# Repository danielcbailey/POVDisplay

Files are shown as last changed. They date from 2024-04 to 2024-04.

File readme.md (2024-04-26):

# POV Display

This project uses a custom PCB with an RP 2040 to control 128 RGB LEDs. The LEDs are driven
by 16 high-speed PWM LED driver ICs. The system is cabable of full-color video playback.

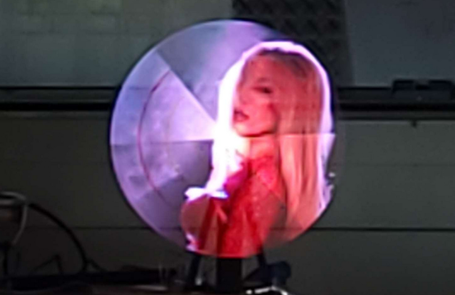
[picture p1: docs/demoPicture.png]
Picture of POV Display in Action


## Sections

[Embedded Software](#embedded-software)

[Video Generation](#video-generation)

[PCB Design](#pcb-design)

[Mechanical Construction](#mechanical-construction)

[Demo Video](#demo-video)

[Known Limitations](#known-limitations)

## Embedded Software

The RP2040 is an ARM M0+ microcontroller with two cores. The embedded software uses both cores
and has one preparing frame buffers while the other sends the data out at the right timing.

The system has two buffers for holding frames and will prepare the next buffer while the current
is read by the other core. The embedded software is designed to be as dumb as possible because
what dumb things lack in intelligence, they have in speed. There are only about 100 clock cycles
between bytes getting written out, so you won't see much code in the embedded software as every
line detracts from the needed speed.

#### File Reading

As such, the file that populates the frame buffers is designed to be as easy as possible for the
embedded code to read and display to the LEDs. The file is set up in such that all it has to do
is read the contents of each frame into the buffer, give a different pointer to each group (more
on this later), and send bytes to each group at the right interval. [Learn more about the binary file format](docs/fileFormat.md)

#### LED Output

The LED output core has three functions: 1. Send data to the right SPI peripheral at a specific
interval. 2. Update the interval based on how fast the board is rotating. 3. Request new frame
buffers when the current is exhausted.

#### Sending Data at a Specific Interval

There are four SPI channels for different regions of LED drivers (see PCB section for motivation).
They are controlled by PIO state machines with FIFO buffers enough to accommodate the entire
burst of data to all four ICs (8 bytes total). Given that bursts are so small but also don't fit
in 32 bits, they aren't well suited for DMA transfer as it would require setting up a new DMA
transfer for every 8 bytes - which comes with the setup overhead.

The RP2040 gives 2 FIFO buffers that can store 4 words of data. In this case, a word is defined
as a single byte, but the RP2040 allows for both FIFOs to be combined into one which allows the
burst to fit into a FIFO. This is key for meeting the timing requirements because the processor
doesn't need to wait for each bit to get written to the wire. By writting to each group's FIFO
buffers 32 bytes at a time, this gives much more headroom for the other activities while still
staying on time.

The actual timekeeping is using the 64-bit system timer which counts for each microsecond that has
passed. Usually, it needs to send a new burst every 25 microseconds, however an even number is
impossible to achieve because the exact timing depends on the rotational speed of the PCB. This
leads to small rounding errors which over the course of a frame consisting of ~41666us can lead to
up to 1.66ms of error in the timing over the course of the frame. This may sound small but it means
the frame can be off by as much as 7.2 degrees which will cause a visual oscillation.

Sub-microsecond precision is needed to stave off these unwanted side effects, and it accomplishes
this by multiplying the timer output by 32 (bit shifted, more precisely by 5 left). This gives 32
times the precision in terms of round-off error. Although floating point logic would eliminate
this need, the floating point calculations alone would easily consume all the clock cycles (3200)
that the loop needs to stay inside.

#### Updating the Interval

No matter the numeric precision of timing is, there will always be some error due to the mechanical
motion. Even a tight PID loop will have *some* error, so the interval update is a little more
complicated than dividing rotational period with number of bursts to write. The software tries to
blend the error so that it speeds up the next frame to make up for a slower current frame, or vice-
versa. This makes error easier on the eyes and looks like a shakey image as opposed to black regions
or chopped-off sections.

The software knows the rotational rate from a hall effect sensor mounted under the PCB. The sensor
provides a digital signal whether the magnet is in range or not, with some hysteresis. The software
measures when the magnet is in range and when it goes out of range. It corrects for the hysteresis
and finds the true center to align the frame vertically.

#### Requesting a New Frame

When the buffers are exhausted, it gets the next buffer filled from the other core. During this time
it applies the updated interval.

## Video Generation

Since the display itself just blindly reads from the file, the difficult task of generating the
video is moved offline to a more powerful computer where real-time conversion isn't necessary. Enter
the video encoder. View the code at tools/videoEncoder

#### Video Input

The encoder accepts any normal cartesian video (as opposed to polar like what it generates) and first
converts it into a series of still frames. This process is almost trivial thanks to [FFmpeg](https://ffmpeg.org/).

#### Frame Encoding

Next, the encoder converts each frame. To improve encoding performance, it does this independently
of previous frames allowing for parallelization. This leads to a decreased quality of output, see more
in the known limitations section.

The encoder simulates the path of the LEDs. It models the position of each one as it steps through
2000 values for angles of the PCB. The LED controller ICs expect packets of 2 bytes each, where the
first byte is the command and the second is the value. This allows us to control any LED and channel
at each step with few constraints.

The value may not be immediately appearent, however imagine that there is a scene with a red dress.
All the channels for each LED is likely to change often, however the red will change more because it
is the dominate color of that portion of the image. This allows us to change the red channel more
often than the others which visually gives a boost of detail and preserves contrast even if not 100%
color accurate.

Not only can it do this per-channel, but it can also do this per-LED for each controller IC. So what
software does is give each timestep a budget to change an LED. As each step passes, the available
budget is incremented by the timestep budget. It evaluates if it has enough budget to change a value
and if so, it samples LED colors and finds the channel that is most desperate to change. It generates
the command/value pair and adds it to the bursts it has generated and decrements the budget. This
mechanism allows it to optimize the bandwidth of the SPI SD card interface while "compressing" the
video.

LEDs are sampled by drawing a small arc representing the LED's path. This arc is drawn in a small
scratch image used for obtaining alpha values for each pixel. It then uses these alpha values to
sample the original image at the corresponding location to form a weighted-average to allow for
anti-aliasing of sorts.

#### Frame Rendering

To preview what the video will look like on the display, the video encoder will render each frame
by reading the sequence of bursts generated as if it were the display. It then draws each arc on
the work-in-progress frame. Since the real display takes advantage of interlacing the LEDs, the
render process will also draw the previous frame interlaced with the current.

These frames are stitched together using FFmpeg to form the preview video.

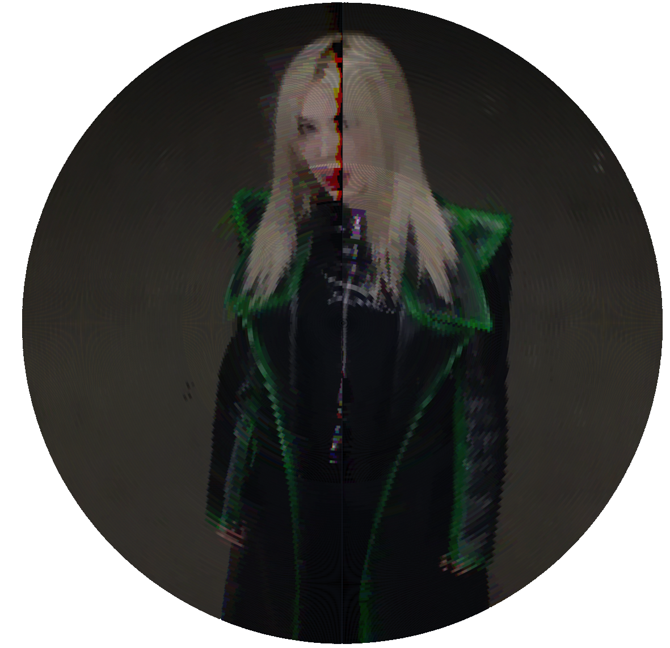
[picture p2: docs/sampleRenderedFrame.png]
Sample Rendered Frame


#### File Generation

Lastly, it generates the output file from the bursts generated during the encoding phase. It builds
the file by adding the headers and keeping to the format outlined [in this format](docs/fileFormat.md).
It does, however, add a small intermediate step. When copying the bursts over, it modifies the values.

The human eye does percieve luminous intensity linearly, rather it is an exponential relationship
where the eye is more sensitive to changes in intensity when light is dim than when it is bright.
The software applies correction for this by sampling from a lookup table and interpolating between
entries.

## PCB Design

The PCB was designed in Altium Designer. You can view the design files in the pcb/ folder. As mentioned,
the design uses an RP2040 at the center. It is connected to a microSD card slot with hardware SPI pins.
A digital hall effect sensor tells the microcontroller when the board has passed the vertical position.

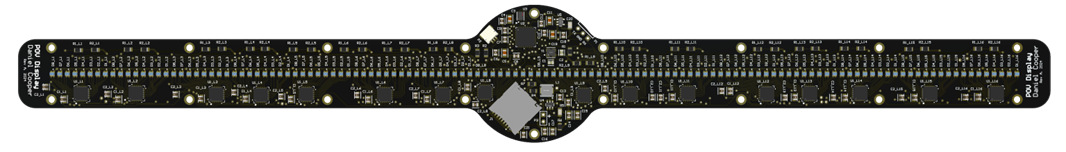
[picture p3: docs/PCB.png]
PCB Render


#### LED Controllers

After conducting an extensive search for LED controller ICs, I settled on the PCA9957HNMP from NXP. It
offers daisy-chain connection, SPI interface (that acts like a shift register while CS is held low), and
most importantly - high speed PWM at 31kHz. Most LED controller ICs have 10+ bit PWM but not only does that
not align well in the memory of the microcontroller, but it makes them slower. The speed comes at the
expense of color quality at low intensities, but speed is most important for a fast-spinning device like
this. The LED controller ICs also have constant current drivers for calibrating the colors and controlling
brightness without sacrificing PWM resolution.

#### Power Rails

The PCB is intended to be powered externally with a device such as a slip ring with 5-6V. A low dropout
linear regulator provides the 3.3V to the digital ICs, and a separate switching regulator provides 3.7V
for the LEDs.

## Mechanical Construction

The mechanical construction is crude, so I won't detail it much. The most notable component is the slip
ring that allows the board to continuously rotate without tangling wires. A small DC motor is connected
with a belt drive to spin the assembly. This DC motor is driven by an external circuit that performs
closed-loop control of the motor using PID. Ideally, a brushless motor would be used with a precision
driver, but I honestly didn't expect the rest of the project to work out as well as it did within the
time constraints.

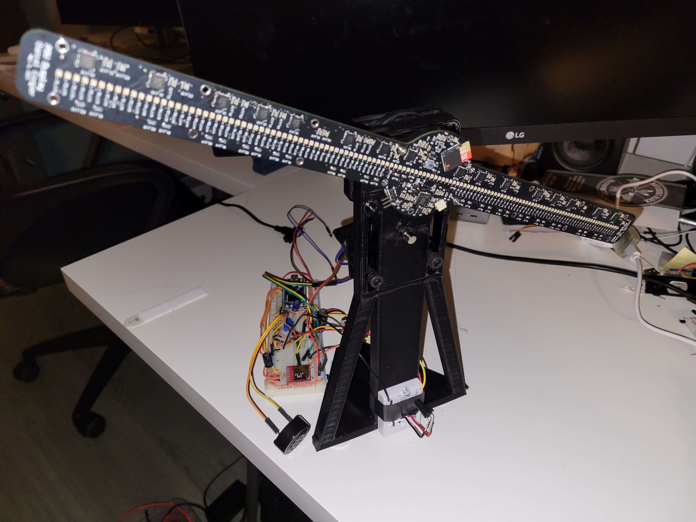
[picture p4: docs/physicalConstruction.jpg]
Mechanical Construction


## Demo Video

Coming soon!

## Known Limitations

Although the project has exceeded my expectations, it does have some notable limitations for those who
come across my work.

* The SPI interface for SD cards is slow (~11Mbps max) and it is the limiting factor for resolution and framerate.
Consider using a microcontroller that has an sdio interface.
* The power traces are not sized properly for the current ripple caused by the LED PWM. Make larger PCB traces and
larger bypass capacitors to not cause excessive ripple on the ground net.
* Consider using a servo motor for precision speed control. The image shakes a little still.
* Instead of using a slip ring, inductive power transfer would be better because I am exceeding the rated speed of
the slip ring by over a factor of two.
* Wireless communication such as WiFi would allow debugging while spinning, and upload of files to high-speed flash
memory (so that the SD card doesn't fly out).
* The PCB doesn't natively interlace the LEDs. I have performed this by mechanically offsetting the PCB, but this
leads to a slight imbalance.

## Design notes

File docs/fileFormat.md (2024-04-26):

# File Format of Video Data

The processor loads the data for the LEDs at any given time from the SD card.
The LEDs are in groups of four, and at any given transfer, one LED from each controller
must get updated. The timing of sending the data out can vary intra-frame and between frames.
This allows for variable resolution where it counts to get around the SD card limitations.

## Format Overview

The file is organized into the following portions:

* File header - details how many frames are in the file.
* Frame - the organizational unit for one complete revolution of the display. Frames contain four groups.
* Group - the organizational unit within one frame that details the data to be sent to one group of LEDs for that frame.
* Packet - the lowest-level container of data, corresponding to data samples and the rotational proportion they represent.

## File Header Format

| Offset | Field |
| --- | ----- |
| 0x0000 | File Format Identifier: "CRV\0" |
| 0x0004 | Number of frames: uint32 |
| 0x0008 | Start of frame 0 |

## Frame Format

| Offset | Field |
| --- | ----- |
| 0x0000 | Group 2 offset: n (uint32) |
| 0x0004 | Group 3 offset: m (uint32) |
| 0x0008 | Group 4 offset: p (uint32) |
| 0x000C | Frame length: uint32 |
| 0x0010 | Start of group 1 |
| n | Start of group 2 |
| m | Start of group 3 |
| p | Start of group 4 |

## Group Format

| Offset | Field |
| --- | ----- |
| 0x0000 | Number of packets: uint32 |
| 0x0004 | Start of packet 0 |

## Packet Format

| Offset | Field |
| --- | ----- |
| 0x0000 | Start of burst 0 |
| 0x0004 | Last bytes of burst 0 |
| 0x0008 | Start of burst 1 |

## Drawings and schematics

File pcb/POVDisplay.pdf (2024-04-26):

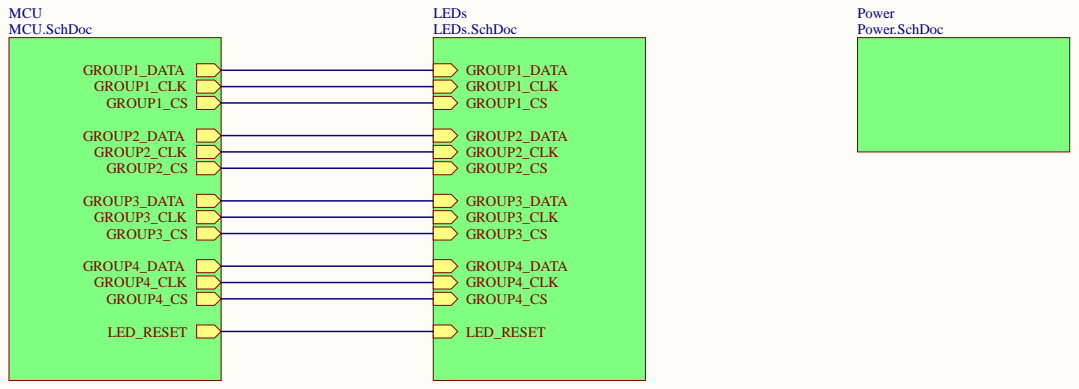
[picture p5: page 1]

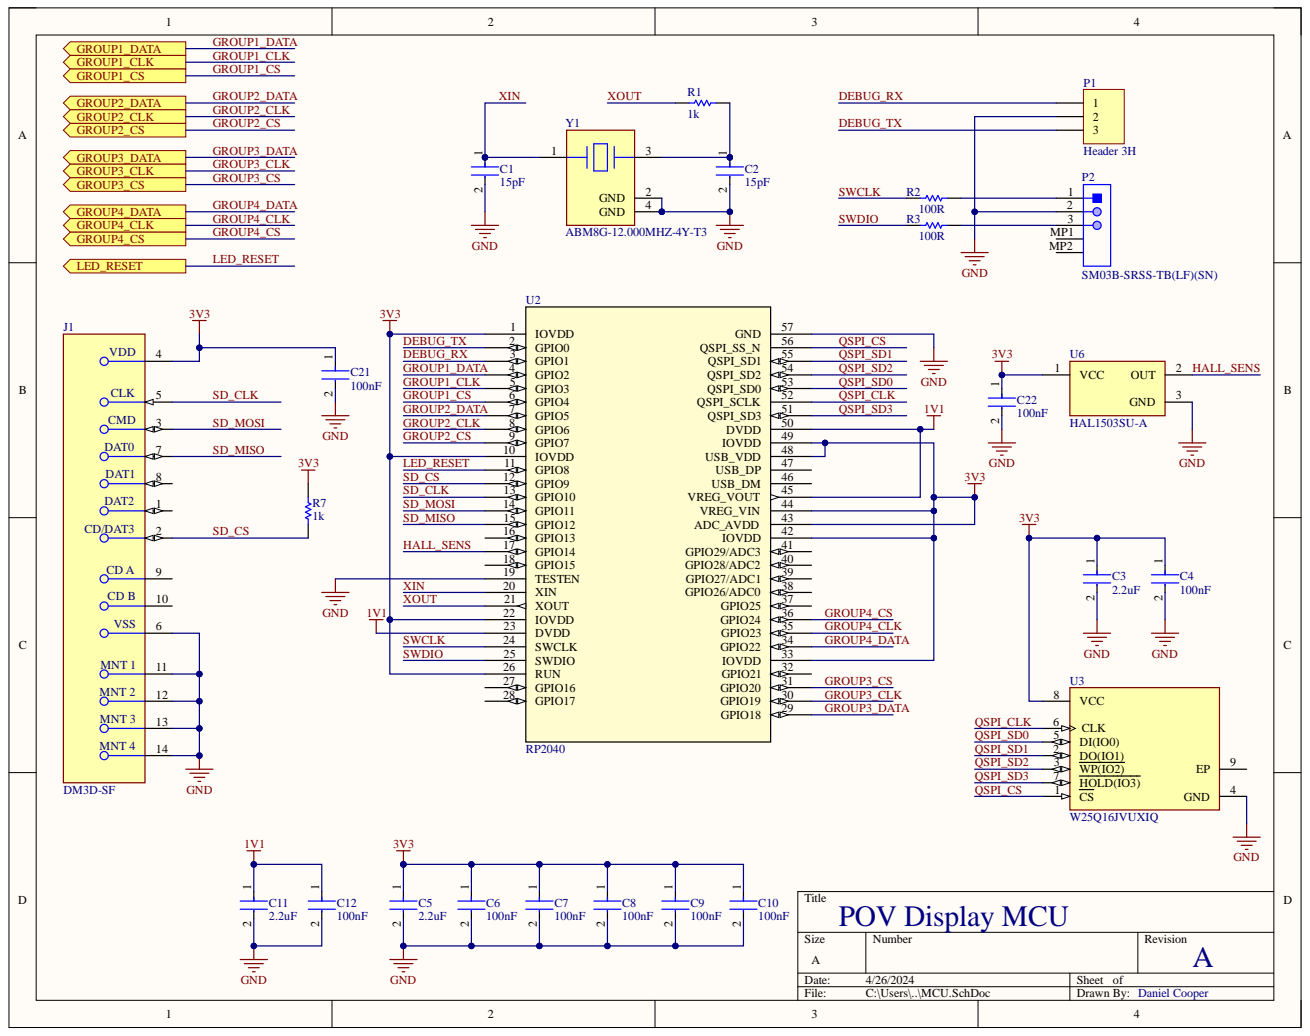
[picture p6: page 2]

SM03B-SRSS-TB(LF)(SN)

DVDD 23

SWCLK | SWCLK 24

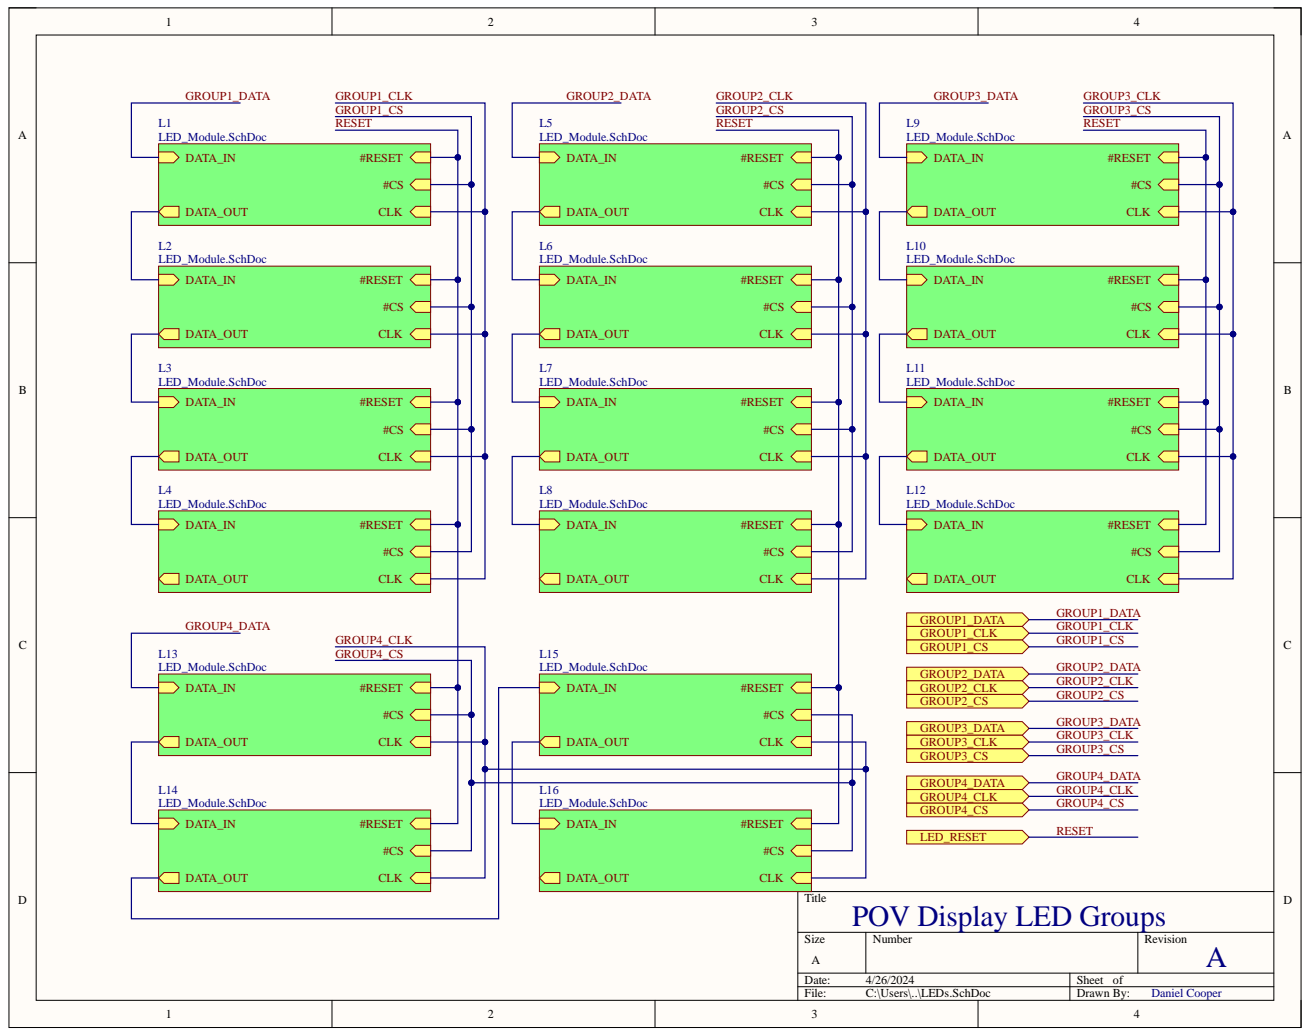
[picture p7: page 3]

Title
POV Display LED Groups

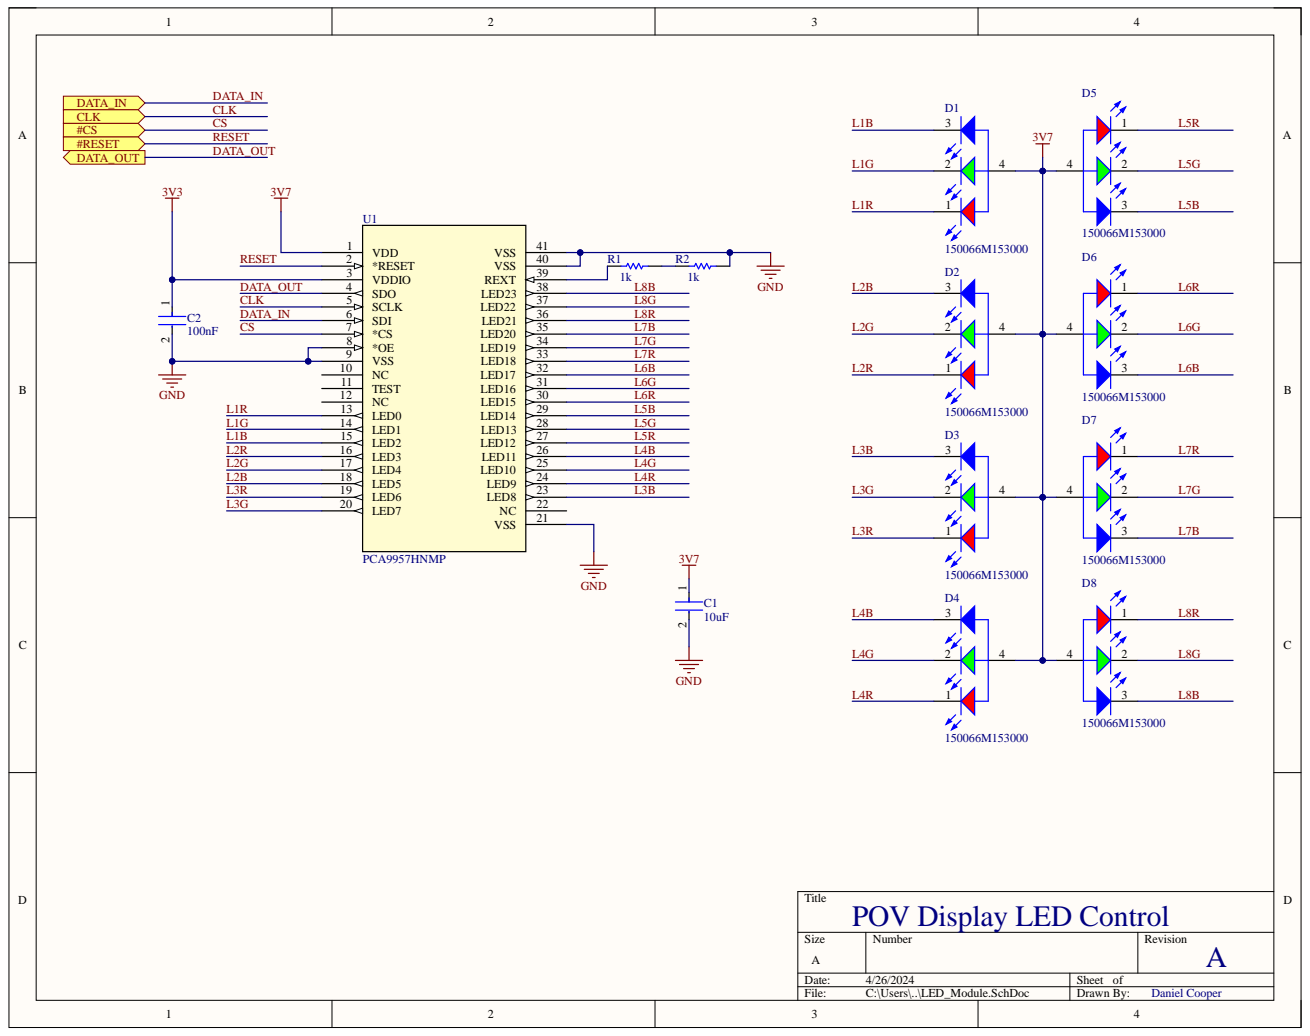
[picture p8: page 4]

POV Display LED Control Dani

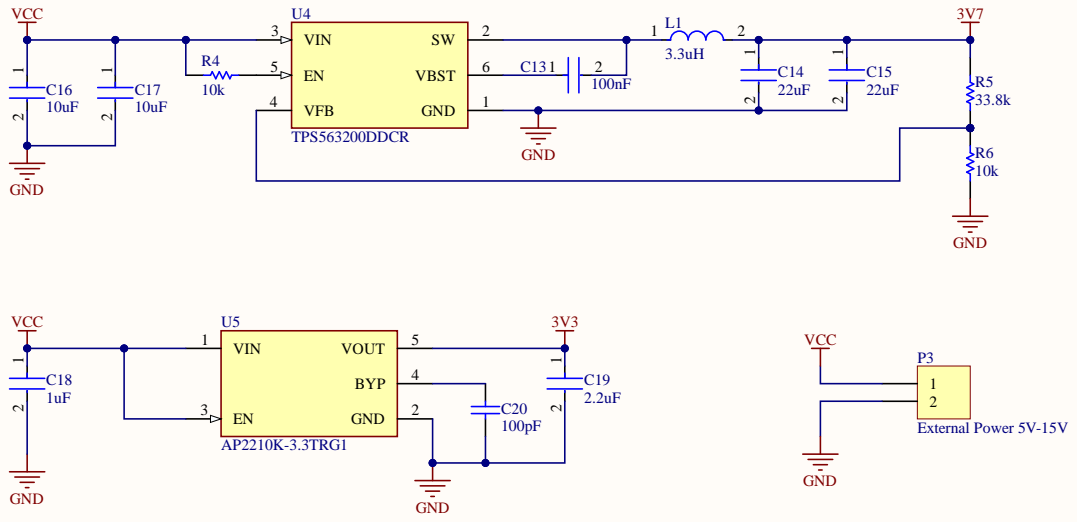
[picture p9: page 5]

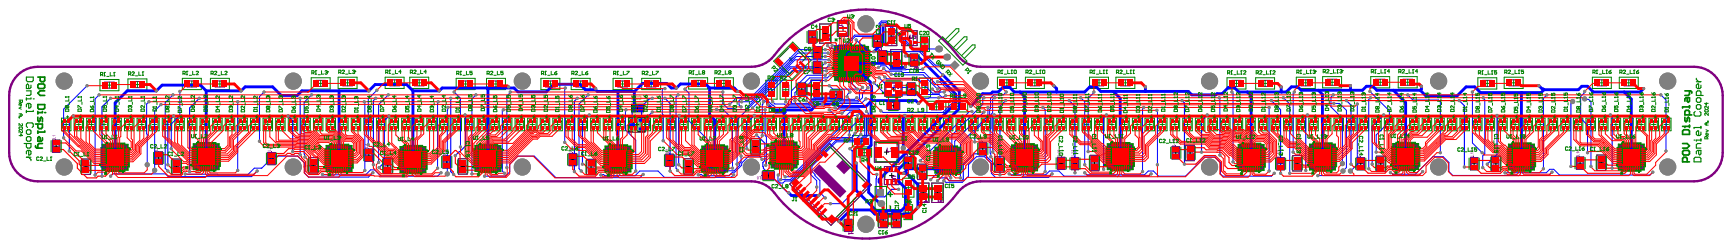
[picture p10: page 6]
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

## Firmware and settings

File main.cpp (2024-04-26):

#include <stdio.h>
#include "pico/stdlib.h"

#include "LEDController.hpp"
#include "videoFileReading.h"
#include "hardware.h"
#include "hw_config.h" // SD card
#include "f_util.h"
#include "ff.h"
#include "pico/multicore.h"

void displayOnLEDs();

int main() {

    // Initialize chosen serial port
    stdio_init_all();
    sd_card_t* pSD = sd_get_by_num(0);
    FRESULT res = f_mount(&pSD->fatfs, pSD->pcName, 1);
    if (res != FR_OK) {
        panic("Error mounting SD card: %d\n", res);
    }

    printf("Starting...\n");

    // start the displayOnLEDs function on core 1
    multicore_launch_core1(displayOnLEDs);

    runFileReader("video.crv");
}

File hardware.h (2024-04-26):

#define GROUP1_DATA_PIN 2
#define GROUP1_CLOCK_PIN 3
#define GROUP1_CHIP_SELECT_PIN 4

#define GROUP2_DATA_PIN 5
#define GROUP2_CLOCK_PIN 6
#define GROUP2_CHIP_SELECT_PIN 7

#define GROUP3_DATA_PIN 18
#define GROUP3_CLOCK_PIN 19
#define GROUP3_CHIP_SELECT_PIN 20

#define GROUP4_DATA_PIN 22
#define GROUP4_CLOCK_PIN 23
#define GROUP4_CHIP_SELECT_PIN 24

#define HALL_SENSOR_PIN 14
#define LED_RESET_PIN 8

#define SD_CARD_CS_PIN 9
#define SD_CARD_CLOCK_PIN 10
#define SD_CARD_MOSI_PIN 11
#define SD_CARD_MISO_PIN 12

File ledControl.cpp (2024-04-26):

#include "videoFileReading.h"
#include "pico/stdlib.h"
#include "pico/types.h"
#include "hardware.h"
#include "LEDController.hpp"
#include <stdio.h>

uint32_t timeBetweenPackets(uint32_t frameTime, uint32_t numPackets) {
    return (frameTime << 5) / numPackets; // the x32 is to allow for fractional microseconds
}

unsigned char* currGroupBuffers[4] = {nullptr, nullptr, nullptr, nullptr};
int currGroupPacketPos[4] = {0, 0, 0, 0};
uint32_t groupTimeBetweenPackets[4] = {0, 0, 0, 0};
uint64_t groupNextPacketTime[4] = {0, 0, 0, 0};
int groupPacketLength[4] = {0, 0, 0, 0};
int numPacketsRetrieved[4] = {0, 0, 0, 0};

unsigned char iRefs[16] = {
    20,
    20,
    20,
    19, // L4
    19,
    18,
    17,
    15, // L8
    15,
    17,
    18,
    19, // L12
    19,
    20,
    20,
    20 // L16
};

// unsigned char iRefs[16] = {
//     30,
//     30,
//     29,
//     29, // L4
//     28,
//     26,
//     24,
//     20, // L8
//     20,
//     24,
//     26,
//     28, // L12
//     29,
//     29,
//     30,
//     30 // L16
// };

float channelScalars[3] = {
    1.7, // Red
    0.4, // Green
    0.8 // Blue
};

unsigned char temp2;

inline uint64_t abs(uint64_t a) {
    return a < 0 ? -a : a;
}

void updateGroupBuffers(uint32_t frameTime);

uint32_t frameTimeBuffer[15]; // circular buffer of frame times
uint32_t frameTimeBufferPos = 0;

uint64_t timeAround = 0;

void displayOnLEDs() {
    sleep_ms(5924); // give the SD card time to initialize

    // Initializing LEDs
    LEDController group1(GROUP1_DATA_PIN, GROUP1_CLOCK_PIN, GROUP1_CHIP_SELECT_PIN);
    LEDController group2(GROUP2_DATA_PIN, GROUP2_CLOCK_PIN, GROUP2_CHIP_SELECT_PIN);
    LEDController group3(GROUP3_DATA_PIN, GROUP3_CLOCK_PIN, GROUP3_CHIP_SELECT_PIN);
    LEDController group4(GROUP4_DATA_PIN, GROUP4_CLOCK_PIN, GROUP4_CHIP_SELECT_PIN);
    LEDController* groups[4] = {&group1, &group2, &group3, &group4};

    // Resetting the LEDs
    gpio_init(LED_RESET_PIN);
    gpio_set_dir(LED_RESET_PIN, GPIO_OUT);
    gpio_put(LED_RESET_PIN, 0);
    sleep_ms(10);
    gpio_put(LED_RESET_PIN, 1);
    sleep_ms(10);

    gpio_init(HALL_SENSOR_PIN);
    gpio_set_dir(HALL_SENSOR_PIN, GPIO_IN); // reads 1 when no magnet, 0 when magnet
    gpio_pull_up(HALL_SENSOR_PIN); // sensor is open-drain

    // initializing the chips
    for (int i = 0; i < 4; i++) {
        for (int j = 0; j < 24; j++) {
            float colorScalar = channelScalars[j % 3];

            // unsigned char buffer[16] = {
            //     (0x28 + j) << 1, iRefs[4*i + 3] * scalar, 
            //     (0x28 + j) << 1, iRefs[4*i + 2] * scalar,
            //     (0x28 + j) << 1, iRefs[4*i + 1] * scalar,
            //     (0x28 + j) << 1, iRefs[4*i] * scalar
            // };

            unsigned char buffer[16];
            for (int k = 0; k < 4; k++) {
                buffer[2*k] = (0x28 + j) << 1;
                int ledIdx = (4*i + (3-k)) * 8 + (7-j / 3);
                float mirroredIdx = ledIdx > 63 ? 127 - ledIdx : ledIdx;
                float posScalar = 64.0f / (mirroredIdx - 67) + 21.0f;

                buffer[2*k + 1] = posScalar * colorScalar;
            }

            groups[i]->sendData(buffer);
            sleep_us(150);
        }
    }

    uint32_t frameTime = 41666; // 12 rotations per second
    uint64_t magnetFrameOnTime = time_us_64();

    // waiting for the bar to be in the right position
    uint64_t prevRotationStart = time_us_64();
    bool wasMagnet = gpio_get(HALL_SENSOR_PIN);
    int count = 0;
    while (true) {
        bool magnetReading = gpio_get(HALL_SENSOR_PIN);
        if (!magnetReading && magnetReading != wasMagnet) {
            magnetFrameOnTime = time_us_64();
        } else if (magnetReading != wasMagnet) {
            wasMagnet = !wasMagnet;
            count++;

            uint64_t currTime = time_us_64();
            uint64_t centerTime = (currTime - magnetFrameOnTime) * 5 / 6 + magnetFrameOnTime;
            uint32_t rotationTime = centerTime - prevRotationStart;
            prevRotationStart = centerTime;

            if (count >= 2) {
                frameTime = rotationTime / 2;
                break;
            }
        }
        wasMagnet = magnetReading;
    }

    for (int i = 0; 15 > i; i++) {
        frameTimeBuffer[i] = frameTime;
    }

    printf("Frame time stabilized. %d\n", frameTime);

    // initializing next burst times
    for (int i = 0; 4 > i; i++) {
        groupNextPacketTime[i] = time_us_64() << 5;
    }

    uint64_t prevTime = time_us_64();

    while (true) {
        uint64_t currTime = time_us_64();
        uint64_t currTimeX32 = currTime << 5;
        timeAround = currTime - prevTime;
        prevTime = currTime;
        bool magnetReading = gpio_get(HALL_SENSOR_PIN);
        if (!magnetReading && magnetReading != wasMagnet) {
            magnetFrameOnTime = time_us_64();
        } else if (magnetReading && magnetReading != wasMagnet) {
            uint64_t currTime = time_us_64();
            uint64_t centerTime = (currTime - magnetFrameOnTime) * 5 / 6 + magnetFrameOnTime;
            uint32_t rotationTime = centerTime - prevRotationStart;
            prevRotationStart = currTime;
            uint32_t immediateFrameTime = rotationTime / 2;

            // update frame time buffer
            // frameTimeBuffer[frameTimeBufferPos] = immediateFrameTime;
            // frameTimeBufferPos = (frameTimeBufferPos + 1) % 15;

            // // calculate the average frame time
            // frameTime = 0;
            // for (int i = 0; 15 > i; i++) {
            //     frameTime += frameTimeBuffer[i];
            // }

            // frameTime /= 15;
            frameTime = immediateFrameTime;
            
            // Dialating the frame time - if it hasn't finished the previous frame, it
            // will make the frame time shorter, and if it has, it will make the frame time longer
            // depending on the amount of error
            if (currGroupPacketPos[0] > groupPacketLength[0] / 2) {
                // still working through the previous frame
                float error = (groupPacketLength[0] - currGroupPacketPos[0] - 1) / (float)groupPacketLength[0];
                frameTime = frameTime / (1 + error/2);
            } else {
                // finished the previous frame - already started the next one
                float error = currGroupPacketPos[0] / (float)groupPacketLength[0];
                frameTime = frameTime * (1 + error);
            }

            // syncing buffers
            // if (currGroupPacketPos[0] > groupPacketLength[0] / 2) {
            //     // if more than half way along, advance to the next buffer, otherwise restart current
            //     updateGroupBuffers(frameTime);
            // } else {
            //     for (int i = 0; 4 > i; i++) {
            //         currGroupPacketPos[i] = 0;
            //     }
            // }
        }
        wasMagnet = magnetReading;
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

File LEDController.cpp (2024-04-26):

#include "LEDController.hpp"
#include "hardware/pio.h"

int LEDController::offset = -1;

LEDController::LEDController(uint mosiPin, uint sckPin, uint csPin) {
    PIO pio = pio0;
    float clkdiv = 8; // just a little under 10MHz.

    // Get the PIO state machine
    uint sm = pio_claim_unused_sm(pio, true);

    if (offset == -1) {
        offset = pio_add_program(pio, &spi_cpha0_cs_program);
    }

    // configuring PIO hardware
    pio_sm_config c = spi_cpha0_cs_program_get_default_config(offset);
    sm_config_set_out_pins(&c, mosiPin, 1);
    sm_config_set_sideset_pins(&c, sckPin);
    sm_config_set_out_shift(&c, false, true, 8);
    sm_config_set_fifo_join(&c, PIO_FIFO_JOIN_TX); // double length tx for 8-word fifo
    sm_config_set_clkdiv(&c, clkdiv);

    pio_sm_set_pins_with_mask(pio, sm, (2u << sckPin), (3u << sckPin) | (1u << sckPin));
    pio_sm_set_pindirs_with_mask(pio, sm, (3u << sckPin) | (1u << mosiPin), (3u << sckPin) | (1u << mosiPin));
    pio_gpio_init(pio, mosiPin);
    pio_gpio_init(pio, sckPin);
    pio_gpio_init(pio, sckPin + 1);
    gpio_set_outover(sckPin, GPIO_OVERRIDE_NORMAL);

    uint entry_point = offset + spi_cpha0_cs_offset_entry_point;
    pio_sm_init(pio, sm, entry_point, &c);
    pio_sm_exec(pio, sm, pio_encode_set(pio_x, 8 - 2));
    pio_sm_exec(pio, sm, pio_encode_set(pio_y, 8 - 2));
    pio_sm_set_enabled(pio, sm, true);

    pio_inst = pio;
    pio_sm = sm;
}

void LEDController::sendData(uint8_t* data) {
    io_rw_8 *fifo = (io_rw_8*)&pio_inst->txf[pio_sm];
    for (int i = 0; i < 8; i++) {
        *fifo = data[i];
    }
}
